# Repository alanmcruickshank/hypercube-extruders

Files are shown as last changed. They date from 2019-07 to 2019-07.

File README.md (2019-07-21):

# Hypercube Extruders
Direct drive and Bowden swappable extruders for the Hypercube design of printer.

Also available on thingiverse: http://www.thingiverse.com/thing:3761366

More details on the design rationale of the direct drive extruder here: http://designingoverload.com/2019/07/21/new-hypercube-extruder-designs/

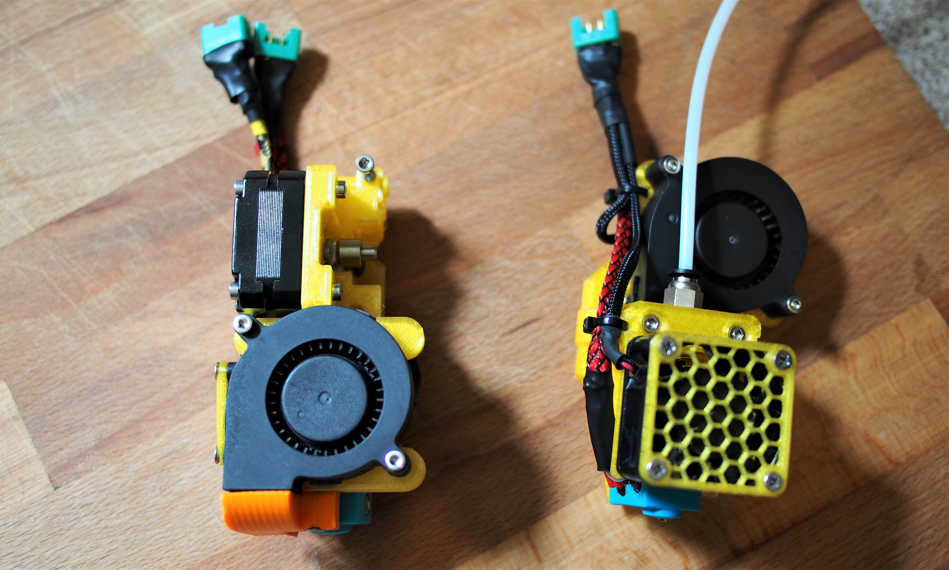
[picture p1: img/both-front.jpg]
Image of both toolheads


### Background
These extruders take a lot of their design inspiration from the [original hypercube
design by Tech2C](https://www.thingiverse.com/thing:1752766). In particular the bowden
extruder is very similar and credit for that original design should go to Tech2C. The
Direct drive extruder is loosely modelled on the PrusaMk3 extruder but with a completely
redesigned idler design.

### Motivations
Both the Bowden and Direct extruders are designed to be swappable on the hypercube, and to
fit within the build volume of a stock designed hypecube without having to move any of the
other parts to make it functional. In particular, working out how to enclose the stepper
motor and blower fans for the Direct Drive extruder was the most tricky. The latter allows
the Hypercube design of printer to print flexible filaments like TPU.

Both extruders use the same print head mounting as Tech2C designed for the orignal hypercube
and are designed to fit to a normal hypercube X-carriage.

Neither of the extruders include an inductive Z probe. They are designed for an AnyCubic
Ultrabase bed (Glass), and so use a Z endstop rather than a probe. Anyone wishing to add a
Z probe mount to the designs, pull requests will be considered, or people are welcome to
duplicate and edit these designs on Thingiverse of fork this repository on Github. Please
link back to this repository or the designs on Github, I'd love to help people find the right
extruder for them.

## Design and Assembly
_All the CAD work is in OpenSCAD to enable people to edit the designs themselves if they like._

Given that these components will be near *heat*, I strongly recomment printing in PETG rather
than PLA. All of these parts have been printed at .2mm layer heights and have worked fine.
Some post processing/cleanup on holes may be required.

The OpenSCAD files also depend on the chamfered primitives library: https://www.thingiverse.com/thing:1305888

### Bowden

This is really just the hotend, you'll need your own extruder. I use the compact bowden extruder
from the original hypercube.

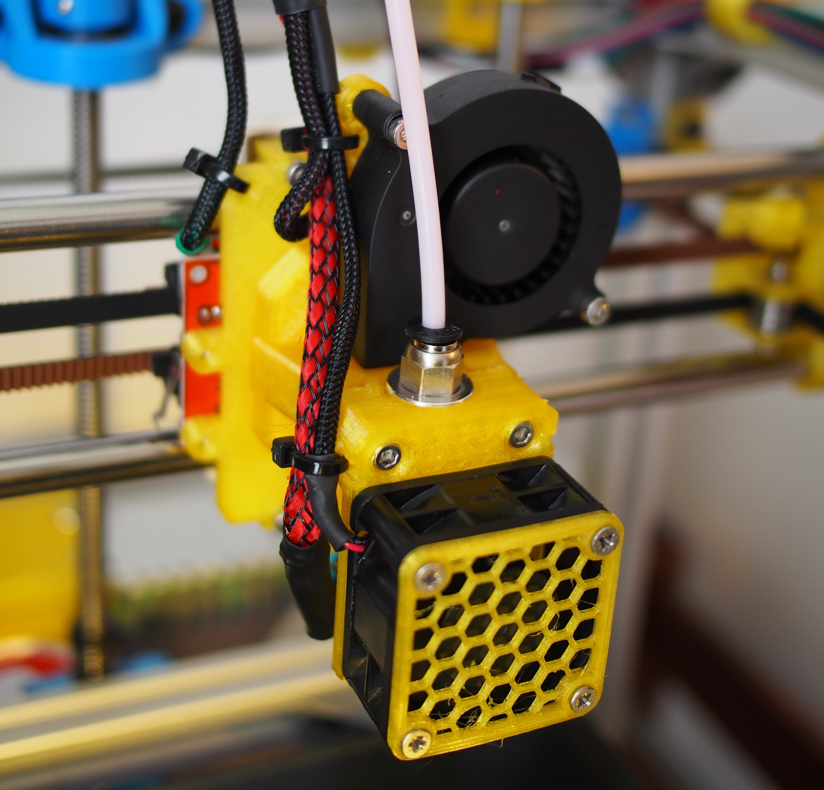
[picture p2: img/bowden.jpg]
Image of bowden on the printer


Components:
- Printed
  - 1x `bowden-toolhead`.
    _NB: This toolhead has an integrated duct, rather than the seperate ducting piece required
    for the original hypercube design. This makes assembly simpler and also makes the design
    lighter._
  - 1x `bowden-clamp-40mm`
  - (optional) 1x 40mm Fan Grille
    from [mightynozzle on Thingiverse](http://www.thingiverse.com/thing:2802474)
- Non Printed
  - 1x E3D V6 hotend (bowden configuration)
  - 4x M3 nyloc nuts (for mounting to the x-carriage)
  - 4x M3 full nuts
    - 2x for mounting the blower fan
    - 2x for attaching the clamp
  - 4x M3x20 Socket Head screws
    - 2x for mounting the blower fan
    - 2x for mounting the clamp
  - 1x Blower fan (same as for Hypercube)
  - 1x 40mm Case Fan (Designed around a Scythe Mini `SY124020L`) which is _really_ quiet, but any
    40mm fan up to 20mm deep fan should work.
  - 4x No4 (2.9mm dia) x 32mm (1 1/4") self tapping screws (to mount the 40mm fan)
  - 2x 2.5mm cable ties
  - (optional) Cable braiding and heatshrink to taste.
  - (optional) 1x MPX M6 connectors (if using these to make the extruders
    swappable as recommended by Tech2C)

### Direct Drive

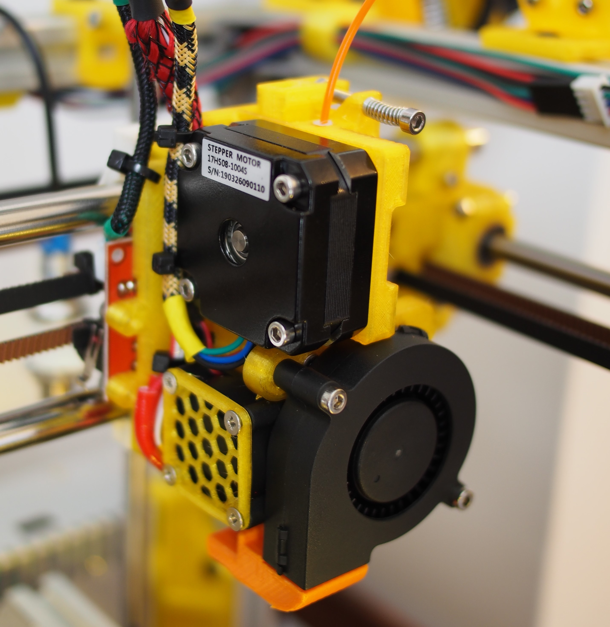
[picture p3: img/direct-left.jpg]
Image of direct version on the printer from the left


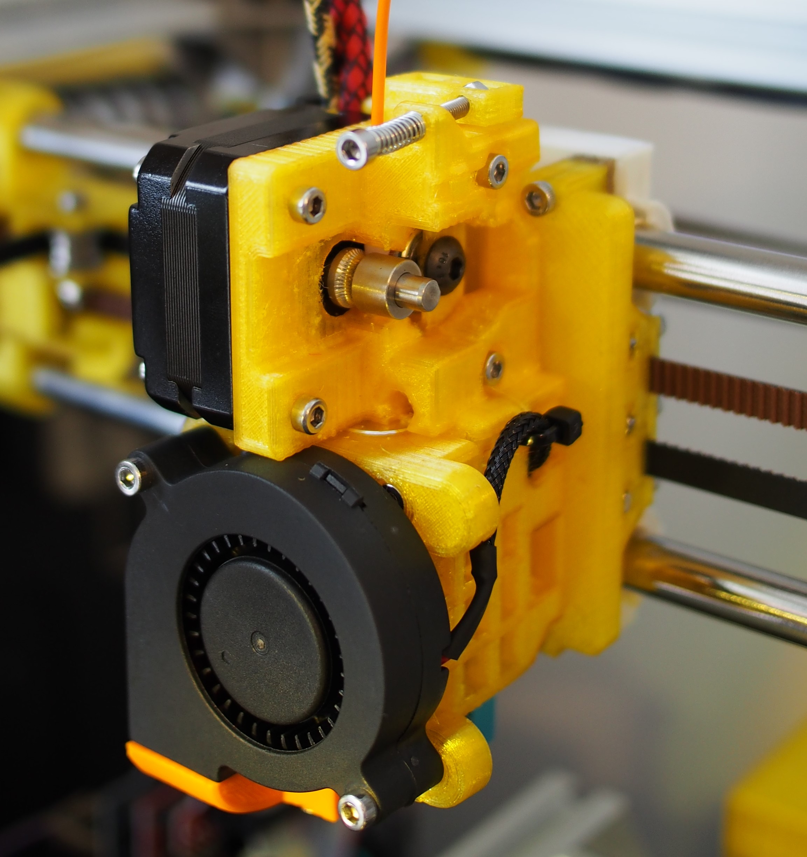
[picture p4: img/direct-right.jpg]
Image of direct version on the printer from the right


Components:
- Printed
  - 1x `direct-toolhead`
  - 1x `direct-duct`
  - 1x `direct-clamp`
  - 1x `direct-idler-arm`
  - 1x `bowden-clamp-40mm`
  - (optional) 1x 30mm Fan Grille
    from [mightynozzle on Thingiverse](http://www.thingiverse.com/thing:2802474)
- Non Printed
  - 1x E3D V6 hotend (direct configuration). *Ideally also drill out the end, to insert
    some PTFE tubing directly down the throad*. A PTFE insert is also helpful.
  - 1x NEMA17 20mm deep stepper motor. This is less deep than the usual NEMA17 stepper
    motors but we need a lower profile one so that we don't hit the frame of the hypercube.
  - 1x 625 bearing
  - 1x M5x10 bolt for holding the bearing (I use half round head, but other style may also
    work).
  - 4x M3 nyloc nuts (for mounting to the x-carriage)
  - 5x M3 full nuts
    - 2x for mounting the blower fan
    - 2x for attaching the clamp
    - 1x for the tensioner arm bolt
  - 6x M3x20 Socket Head screws
    - 2x for mounting the blower fan
    - 2x for mounting the clamp
    - 2x for the stepper motor (one of which is also the axle for the idler arm).
  - 2x M3x10 Socket Head screws (for the other two mounting points for the stepper motor).
  - 1x M3x30 Socket Head screw for the tensioning arm.
  - 1x The spring from a biro, to go around the M3x30 bolt.
  - 1x Blower fan (same as for Hypercube)
  - 1x 30mm Fan, no more than 10mm deep
  - 5x No4 (2.9mm dia) x 19mm (3/4") self tapping screws
    - 4x to mount the 30mm fan
    - 1x to mount the duct to the base
  - 4x 2.5mm cable ties
  - (optional) Cable braiding and heatshrink to taste.
  - (optional) 2x MPX M6 connectors (if using these to make the extruders
    swappable as recommended by Tech2C)
    - One for the same configuration as the bowden setup, one for a
      line to the stepper motor

### Mounting Point (2020 extrusion)

If you've got two print heads, it's useful to have somewhere to put the ones you're not using. This is a simple solution to that problem.

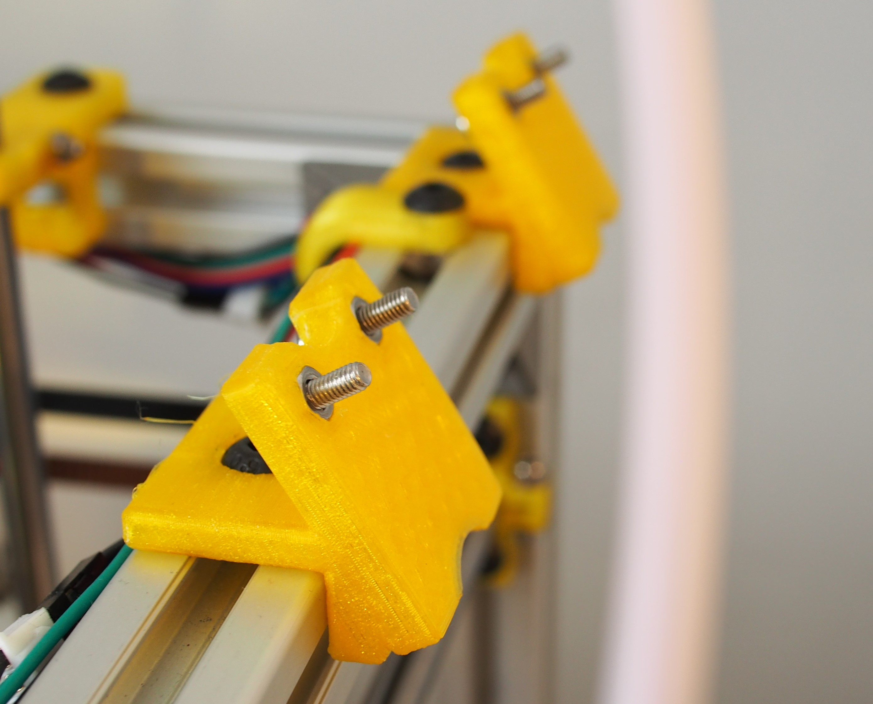
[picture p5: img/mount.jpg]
Image of mount


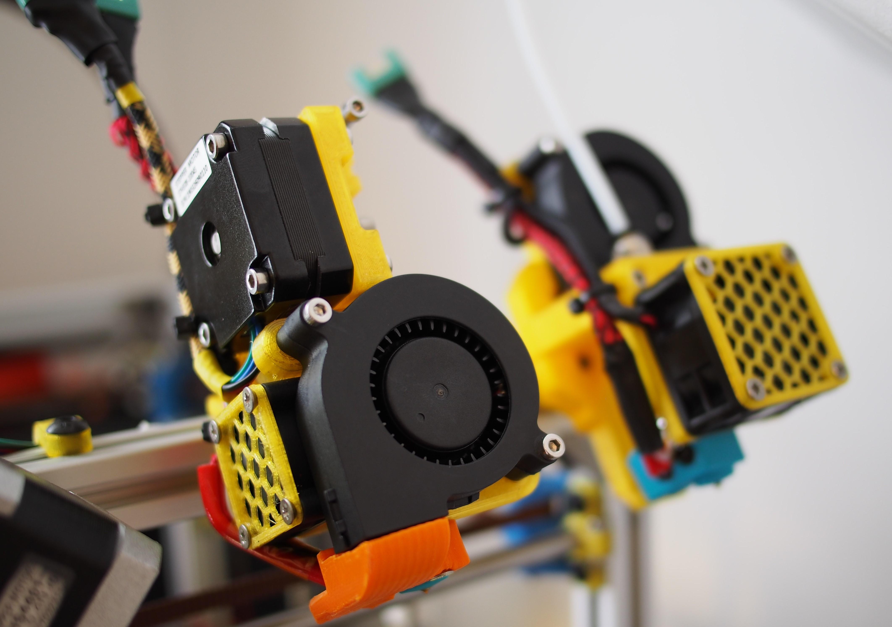
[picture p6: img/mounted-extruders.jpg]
Image of mounted extruders


Components:
- Printed
  - 1x `mount`
- Non Printed
  - 1x M5x8 bolt
  - 1x M5 T-nut
  - 2x M3 full nuts
  - 2x M3x10 Socket Head screws

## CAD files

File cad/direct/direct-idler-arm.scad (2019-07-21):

use <Chamfers-for-OpenSCAD/Chamfer.scad>;

$fs = 0.01;

/// Bearing Arm
// motor mount screws at 31mm apart and mounted with M3 screws

armBalance();

module armBalance(){
    difference(){
        union(){
            difference(){
                union(){
                    translate([-12,-5,-4]) chamferCube(36,10,10,0.5);
                    intersection(){ // clever chamfering
                        translate([-18.5,-5,-4]) chamferCube(32,10,10,0.5);
                        translate([-18.5,-10,-6]) chamferCube(32,20,12,4);
                    }
                    translate([0,-5,2]) scale([1,1,0.8]) rotate([-90,0,0]) cylinder(d=14, h=10);
                    // horizontal end
                    translate([23,-15,-4]) chamferCube(5,20,10,0.5);
                }
                translate([-9,-3.5,-20]) chamferCube(18,7,40,0.5);
            }
            translate([0,-3.5,3]) rotate([-90,0,0]) cylinder(d=8, h=1);
            translate([0,2.5,3]) rotate([-90,0,0]) cylinder(d=8, h=1);
        }
        translate([0,-10,3]) rotate([-90,0,0]) cylinder(d=4.8, h=20); // Snug M5 fit so no nut required
        translate([-15.5,-10,0]) rotate([-90,0,0]) cylinder(d=3.6, h=20); // slack M3 fit
        // slack slot for other moving bolt
        translate([15.5-2.5,-6,-3]) chamferCube(5,12,7,0.5);
        // top gap
        translate([11.5,-6,5]) chamferCube(12,12,8,0.5);
        // weight saving
        translate([15.5+2.5-3,-3,-2]) chamferCube(30,6,5,0.5); // lower
        
        translate([15.5+2.5+3,-3-10,-2]) chamferCube(30,6,5.5,0.5); // side (and tube gap)
        translate([23+2.5-1.8,-3-10,0]) chamferCube(3.6,6,4,0.5); // side (and tube gap)
        // tension hole
        translate([23+2.5,0,8]) cylinder(d=3.4, h=12);
        translate([23+2.5,-10,0]) cylinder(d=3.6, h=12);
    }
}

module 605_bearing(){
    difference(){
        rotate([-90,0,0]) translate([0,0,-2.5]) chamferCylinder(5,8,8,0.5);
        rotate([-90,0,0]) translate([0,0,-2.5]) chamferCylinder(5,2.5,2.5,-0.5);
    }
}

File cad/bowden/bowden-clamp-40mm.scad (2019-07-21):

use <Chamfers-for-OpenSCAD/Chamfer.scad>;

$fs = 0.01;

difference () {
    union () {
        chamferCube(38,12,13,1);
        // cable tie lugs (upper)
        translate([-2,4,4]) chamferCube(42,7,5,1);
        // struts
        translate([-1,0,0]) chamferCube(8,40,12,1);
        translate([31,0,0]) chamferCube(8,40,12,1);
        // struts (long)
        translate([-1,0,0]) chamferCube(8,50,8,1);
        translate([31,0,0]) chamferCube(8,50,8,1);
        // fan ducting (joins)
        translate([19-(23/2)-3,10,0]) chamferCube(3,10,12,1);
        translate([19+(23/2),10,0]) chamferCube(3,10,12,1);
        // fan ducting
        translate([19-(23/2)-3,12,0]) chamferCube(3,28,17,1);
        translate([19+(23/2),12,0]) chamferCube(3,28,17,1);
        // base ducting
        translate([4,44,0]) chamferCube(30,6,2,1);
    }
    // screw holes
    translate([6,6,0]) chamferCylinder(13, 1.5, 1.5, -0.5);
    translate([38-6,6,0]) chamferCylinder(13, 1.5, 1.5, -0.5);
    // cable tie holes
    translate([-1,6,0]) cube([1.5,3,20]);
    translate([37.5,6,0]) cube([1.5,3,20]);
    
    // screw head holes (incl slight conical recess)
    translate([6,6,0]) chamferCylinder(3, 6.5/2, 2, -0.5);
    translate([38-6,6,0]) chamferCylinder(3, 6.5/2, 2, -0.5);
    translate([6,6,0]) cylinder(h=3, d=6.5);
    translate([6,6,3]) cylinder(h=1, d1=6.5, d2=3);
    translate([38-6,6,0]) cylinder(h=3, d=6.5);
    translate([38-6,6,3]) cylinder(h=1, d1=6.5, d2=3);
    
    // E3D Mount
    translate([19,0,13]) rotate([-90,0,0])union() {
        translate([0,0,9])cylinder(h=3, d=16.2);
        translate([0,0,-1]) cylinder(h=5, d=16.2);
        cylinder(h=12, d=12.2);
    }
    
    // fan mount holes
    // 2.7mm dia
    translate([19-16,14,0]) cylinder(h=20, d=2.7);
    translate([19+16,14,0]) cylinder(h=20, d=2.7);
    translate([19-16,14+32,0]) cylinder(h=20, d=2.7);
    translate([19+16,14+32,0]) cylinder(h=20, d=2.7);
    
    translate([-5,0,0]) linear_extrude(height=12) polygon([[0,0],[7,0],[0,7]]);
    translate([37+6,0,0]) linear_extrude(height=12) polygon([[0,0],[-7,0],[0,7]]);
    
    // beautification lofts
    translate([-3,12,0]) rotate([0,30,0]) translate([-8,0,0]) chamferCube(8,50,20,1);
    translate([41,12,0]) rotate([0,-30,0]) translate([0,0,0]) chamferCube(8,50,20,1);
    translate([-3,52,0]) rotate([30,0,0]) translate([-8,0,0]) chamferCube(80,50,20,1);
    //translate([31,0,0]) chamferCube(8,50,12,1);
}

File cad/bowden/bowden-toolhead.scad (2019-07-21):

use <Chamfers-for-OpenSCAD/Chamfer.scad>;

$fs = 0.01;

c_dist = 30; // distance from base to centreline of hotend.

difference () {
    union () {
        // Baseplate
        intersection(){
            translate([-23,-17,0]) chamferCube(46,46,7,0.5);
            translate([-23,-17,-10]) chamferCube(46,46,27,8);
        }
        intersection(){
            translate([-15,-22,0]) chamferCube(30,10,7,0.5); // baseplate extension
            translate([-15,-22,-10]) chamferCube(30,10,27,2); // baseplate extension
        }
        // E3d Boss
        translate([-19,0,0]) chamferCube(38,12,c_dist,1);
        // E3D Boss Struts
        translate([-17,0,0]) rotate([0,15,0]) translate([-8,0,0]) chamferCube(8,12,24,1);
        translate([17,0,0]) rotate([0,-15,0]) translate([0,0,0]) chamferCube(8,12,24,1);
        // Top Fan mount
        translate([-5.5,46+11,0]) chamferCylinder(7,5,5,0);
        translate([-5.5-4,20,0]) chamferCube(8,37.5,7,0.5);
        
        // Right Fan mount
        translate([38.1,5.8+13,0]) chamferCylinder(7,5,5,0);
        translate([10,5.8+13-4,0]) chamferCube(28.5,8,7,0.5);
        
        // Fan Duct
        // - upper straight duct
        translate([-5,-7,0]) cube([10,7,15]);
        // - mid flange duct
        translate([0,-7,0]) rotate([90,0,0])
            linear_extrude(height=10, scale=[2,0.46])
                translate([-5,0,0]) square([10,15]);
        // - lower main duct
        translate([-10,-50,0]) cube([20,43,7]);
        
        // End Nozzle
        translate([0,-48,7])
            linear_extrude(height=3, scale=[1,0.5])
                translate([-10,0,0]) square([20,7]);
    }
    // screw holes
    translate([-13,6,0]) chamferCylinder(c_dist, 1.7, 1.7, -0.5);
    translate([13,6,0]) chamferCylinder(c_dist, 1.7, 1.7, -0.5);
    // Nut Slots
    translate([-13-(5.6/2),6-3.2,c_dist-5.5]) cube([5.6, 20, 2.8]);
    translate([13-(5.6/2),6-3.2,c_dist-5.5]) cube([5.6, 20, 2.8]);
    
    translate([-13-(5.6/2),6-1.7,c_dist-5.5]) cube([5.6, 3.4, 3.2]);
    translate([13-(5.6/2),6-1.7,c_dist-5.5]) cube([5.6, 3.4, 3.2]);
    
    // Top Fan mount
    translate([-5.5,46+11,0]) cylinder(d=3.4, h=10);
    translate([-5.5,46+11,0]) cylinder(d=6.5, h=4, $fn=6);
    translate([-5.5,46+11,0]) cube([3.4,5.5,8.8], center=true);
    translate([-7.5,46+11-8,0]) cube([1.5,3.5,20]); // cable tie mount
    translate([-10,35,4]) cube([20,6,5]); // blower fan cable duct
    // Right Fan mount
    translate([38.1,5.8+13,0]) cylinder(d=3.4, h=10);
    translate([38.1,5.8+13,0]) cylinder(d=6.5, h=4, $fn=6);
    translate([38.1,5.8+13,0]) cube([3.4,5.5,8.8], center=true);
    
    // Head mount screws
    translate([17/2,-3.5,0]) cylinder(d=3.4, h=10);
    translate([-17/2,-3.5,0]) cylinder(d=3.4, h=10);
    translate([17/2,-3.5,3]) rotate([0,0,90]) cylinder(d=6.5, h=6, $fn=6);
    translate([-17/2,-3.5,3]) rotate([0,0,90]) cylinder(d=6.5, h=6, $fn=6);
    translate([17/2,15.5,0]) cylinder(d=3.4, h=10);
    translate([-17/2,15.5,0]) cylinder(d=3.4, h=10);
    translate([17/2,15.5,3]) rotate([0,0,90]) cylinder(d=6.5, h=6, $fn=6);
    translate([-17/2,15.5,3]) rotate([0,0,90]) cylinder(d=6.5, h=6, $fn=6);
    
    // E3D Mount
    translate([0,0,c_dist]) rotate([-90,0,0])union() {
        translate([0,0,9])cylinder(h=3, d=16.2);
        translate([0,0,-1]) cylinder(h=5, d=16.2);
        cylinder(h=12, d=12.2);
    }
    
    // Fan Ducting (top should be 45 down, bottom should only be 12 deep (at 25 deep)
    // - top entry flange
    translate([-9,11.5,8]) cube([18,1,12]);
    // - upper flange
    translate([0,12,7+7.5+50]) rotate([90,0,0])
        linear_extrude(height=12, scale=[0.45,1.14])
            translate([-9,-56,0]) square([18,12]);
    // - upper duct
    translate([-4,-7,1]) cube([8,7.5,13]);
    // - upper flange
    translate([0,-7,1]) rotate([90,0,0])
        linear_extrude(height=10, scale=[2.2,0.38])
            translate([-4,0,0]) square([8,13]);
    // - lower main duct
    translate([-9,-41,1]) cube([8.5,28,5]);
    translate([0.5,-41,1]) cube([8.5,28,5]);
    
    // bottom duct
    translate([-9,-38.5,3]) rotate([135,0,0]) cube([18,9,3]);
    // bottom cutoff
    translate([-11,-41,0]) rotate([135,0,0]) cube([22,26,10]);
    translate([-11,-50,4]) rotate([45,0,0]) cube([22,26,10]);
    
    // End Nozzle
    translate([0,-47,7])
        linear_extrude(height=3.5, scale=[1,0.3])
            translate([-9,0,0]) square([18,4.5]);
}

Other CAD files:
cad/direct/direct-clamp.scad
cad/direct/direct-duct.scad
cad/direct/direct-toolhead.scad
cad/mount/mount.scad

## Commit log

2019-07-21 Add the bulk of the detail - v1
    [bowden-clamp-40mm.scad, bowden-toolhead.scad, direct-clamp.scad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]
2019-07-21 Ignore STL files
2019-07-21 Add mount and reference to thingiverse
    [mount.scad]
2019-07-21 add the duct mounting screw
